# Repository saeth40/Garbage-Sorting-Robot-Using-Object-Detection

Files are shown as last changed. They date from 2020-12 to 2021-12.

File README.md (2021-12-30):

# Garbage-Sorting-Robot-Using-Object-Detection
2103499 Mechanical Engineering Project, Chulalongkorn University  2019-2020

***Advisor:*** Associate Professor Gridsada Phanomchoeng

***Objective:*** Improve the waste management in Thailand by creating a user-friendly robot that can automatically classify various types of garbage with high accuracy and work fast.

### A short demo VDO: [Click here](https://www.youtube.com/watch?v=DpFVvP5Zfqo).

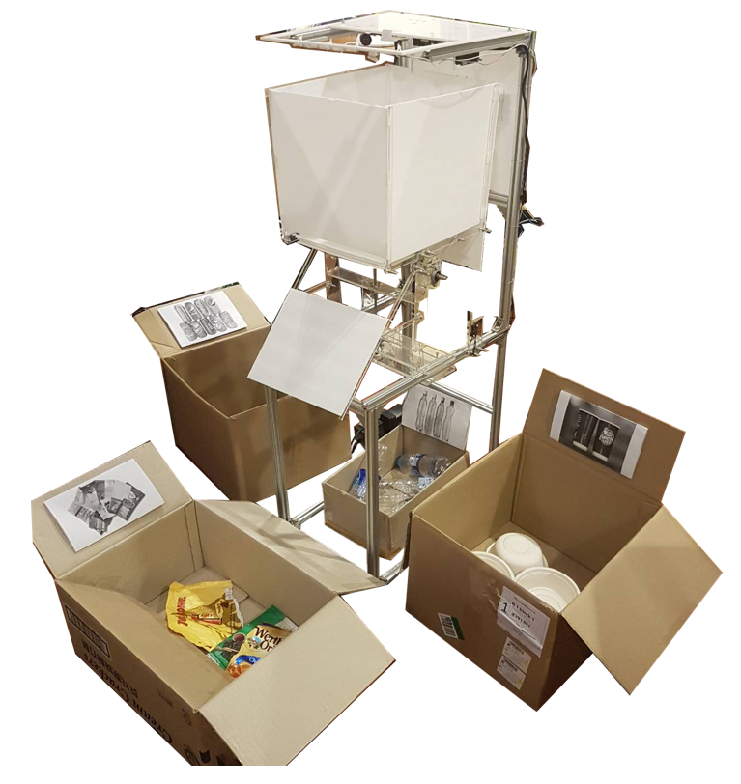
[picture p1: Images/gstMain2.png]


## Data collection
### 1. Types of garbage

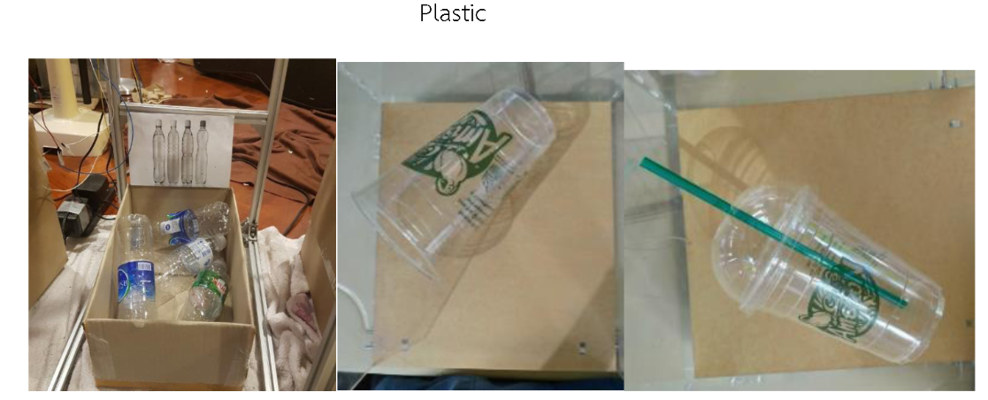
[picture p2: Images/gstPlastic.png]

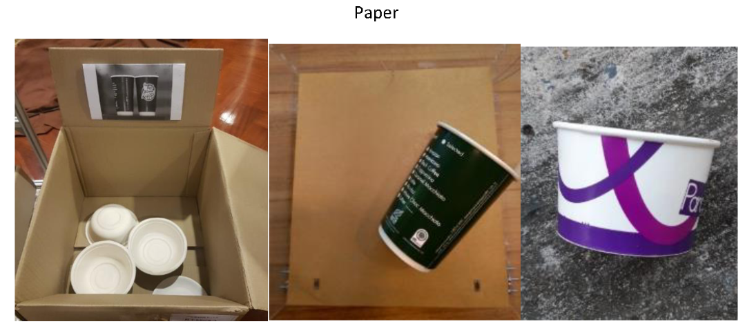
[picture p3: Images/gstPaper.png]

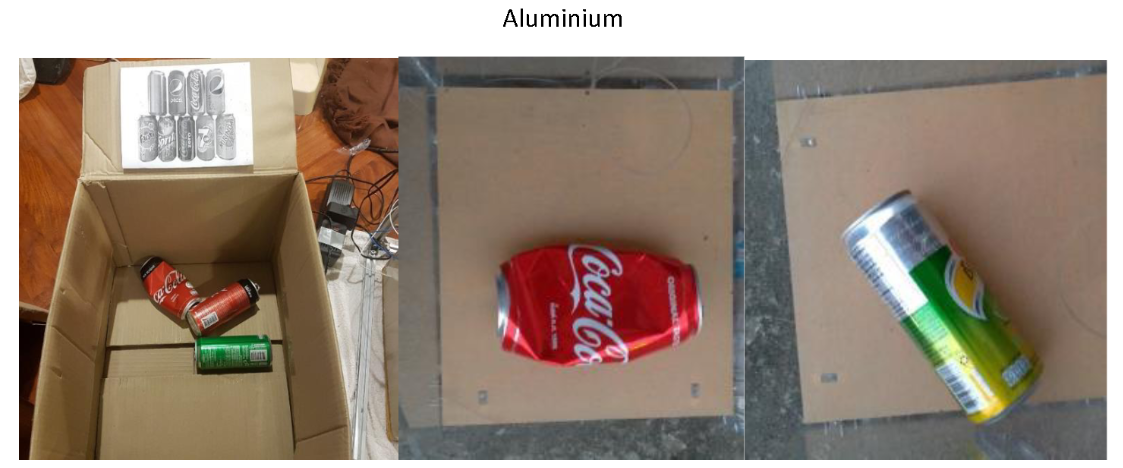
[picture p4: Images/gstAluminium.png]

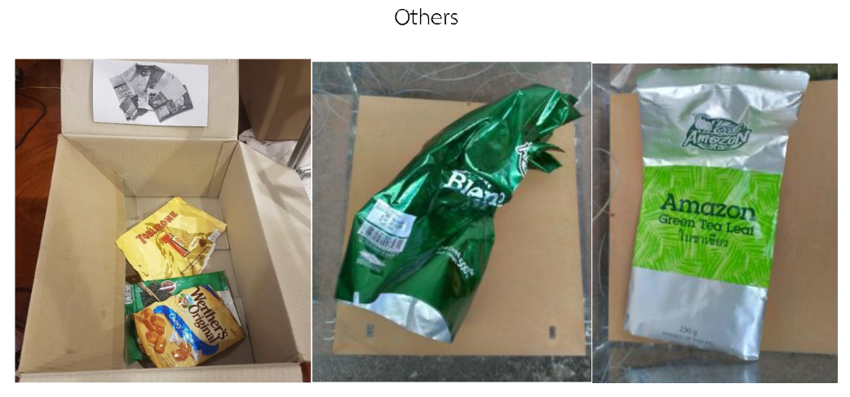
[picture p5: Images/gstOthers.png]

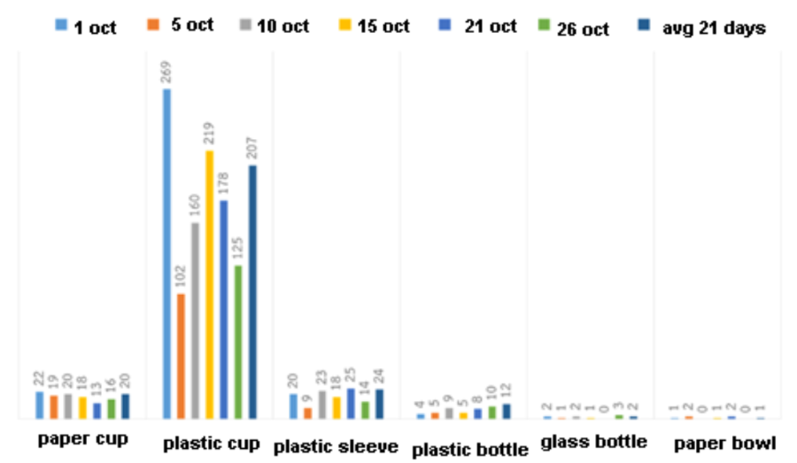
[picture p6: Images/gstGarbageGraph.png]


### 2. Users' preferences

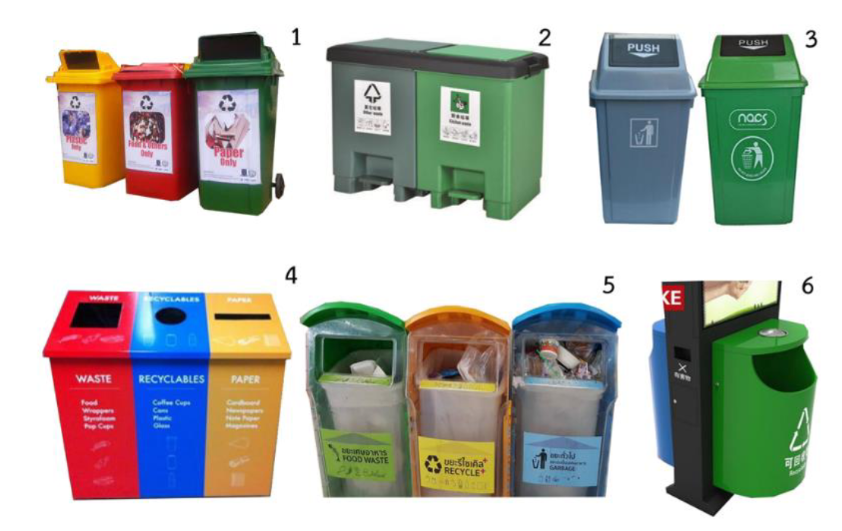
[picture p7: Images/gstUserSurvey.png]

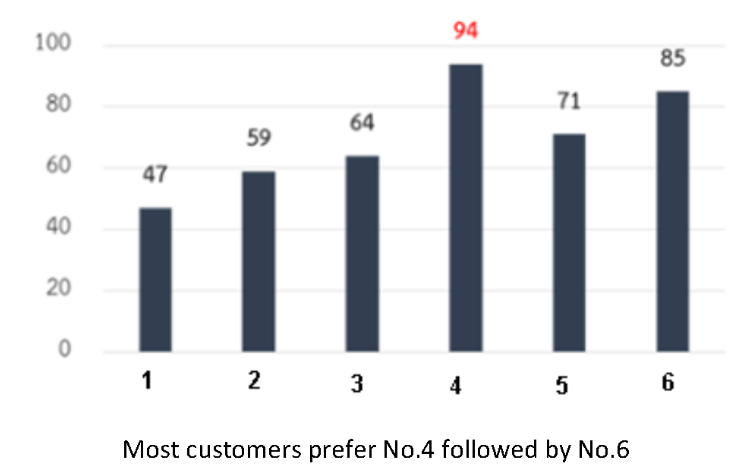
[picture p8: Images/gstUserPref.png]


### All details: [Data collection](https://github.com/saeth40/Garbage-Sorting-Robot-Using-Object-Detection/tree/main/Survey%20data)

## Design the robot

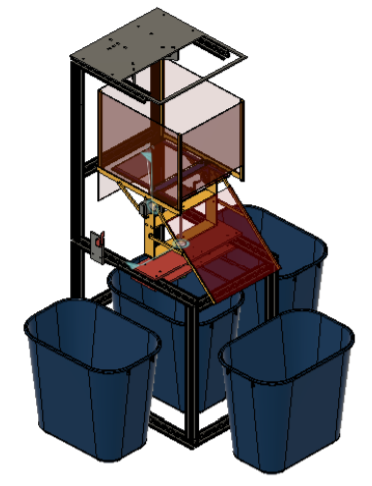
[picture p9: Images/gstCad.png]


### All details:
1. [related research papers](https://github.com/saeth40/Garbage-Sorting-Robot-Using-Object-Detection/tree/main/Related%20research%20papers)
2. [CAD design](https://github.com/saeth40/Garbage-Sorting-Robot-Using-Object-Detection/tree/main/CAD)
3. [List of equipment](https://github.com/saeth40/Garbage-Sorting-Robot-Using-Object-Detection/tree/main/Equipment)

## Programing and testing
### Training and testing object detection with Netpie IoT server to track system's behaviour

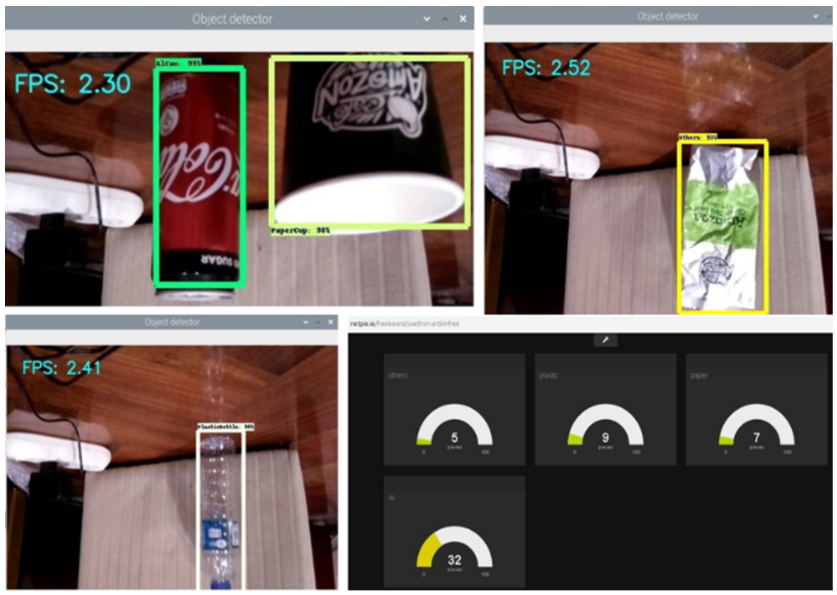
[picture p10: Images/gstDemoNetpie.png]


### Deploying model in the robot

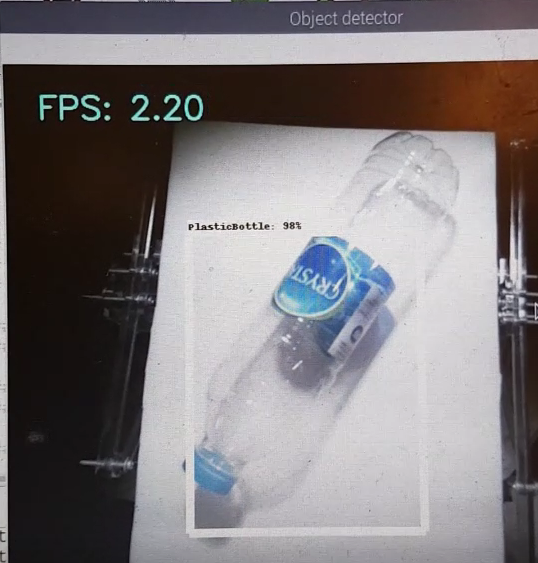
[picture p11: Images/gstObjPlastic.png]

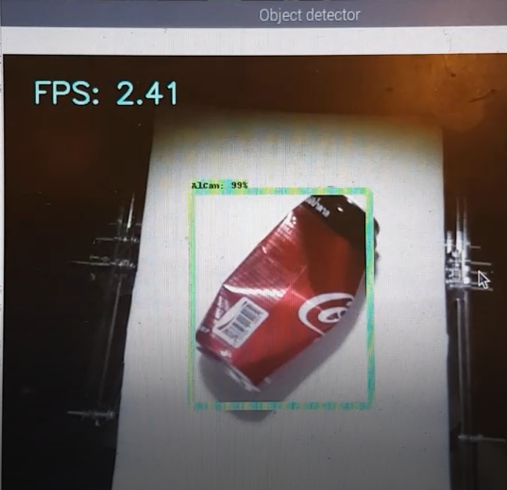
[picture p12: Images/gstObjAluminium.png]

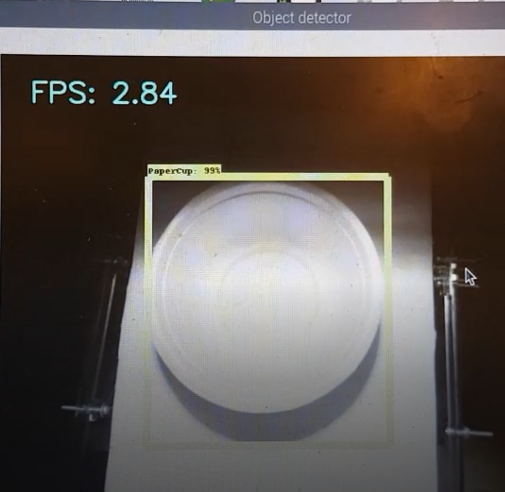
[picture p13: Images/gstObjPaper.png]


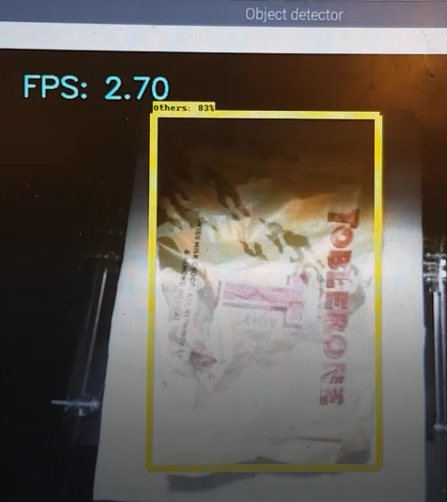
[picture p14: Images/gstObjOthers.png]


### All details
1. [Flowchart and wiring diagram](https://github.com/saeth40/Garbage-Sorting-Robot-Using-Object-Detection/tree/main/Flowchart%20and%20wiring%20diagram)
2. [C++ in Arduino to control sensors and actuators](https://github.com/saeth40/Garbage-Sorting-Robot-Using-Object-Detection/tree/main/C%20%2B%2B)
3. [Python to train and deploy object detection with IoT server](https://github.com/saeth40/Garbage-Sorting-Robot-Using-Object-Detection/tree/main/Python)
4. [Models used in this project](https://github.com/saeth40/Garbage-Sorting-Robot-Using-Object-Detection/tree/main/Python)
5. [Test results](https://github.com/saeth40/Garbage-Sorting-Robot-Using-Object-Detection/tree/main/Result)

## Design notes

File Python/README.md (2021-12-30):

# Object_detection_picamera

= sending the robot's data to NETPIE server + sending signals to Arduino

# objectDetecttionWithoutNETPIEwithOutGPIO

= not sending the robot's data to NETPIE server and not sending signals to Arduino

# objectDetecttionWithoutNETPIEwithGPIO

= sending the robot's data to NETPIE server but not sending signals to Arduino

# object_detection_tutorial

= tutorial in: https://github.com/saeth40/object_detection_demo

# Train_object_detection

= train the model used in this project

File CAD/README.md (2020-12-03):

You can open CAD files via Fusion360

The pdf file is the images of the CAD files and the real robot

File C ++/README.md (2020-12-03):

Open in Arduino IDE

You can download it from: https://www.arduino.cc/en/software 

This code is used in Arduino MEGA to communicate with Raspberry pi and control sensors and actuators

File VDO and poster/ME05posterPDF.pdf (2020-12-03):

# GARBAGE SORTER ROBOT FOR CAFÉ AMAZON

Saeth Wannasuphoprasit 5930504121 | Krittakorn Dilokpakin 5930009921 | Sittipat Kositpon 5930524721

### Associate Professor Gridsada Phanomchoeng, Ph.D. (Adviser) Department of Mechanical Engineering, Faculty of Engineering, Chulalongkorn University

The objective of this project is to design and build a trash separating robot with an image processing technique to identify types of trash. In this project, we mainly focus on the trash in café Amazon because of a huge amount and variety of trash along with an inappropriate waste management which leads to environmental degradation. Surveying types and quantity of trash in the actual location along with inspecting how people use bins, we can design the robot and identify types of trash to be separated by the robot. According to the pollution control department in Thailand, types of trash include compostable waste, recycle waste, non-degradable waste and dangerous waste.

## ABSTRACT

## Introduction

# HYULIC SYSTEM DESIGN

# RESULTS

Waste management is one of the biggest problems in the world. There are 14 million tons of trash per day in Thailand but approximately 70 percent of it are not managed and eliminated properly [1]. As a result, serious environment problems occur including air pollution from burnt trash, water pollution which are contaminated by trash, diseases spreading from dirty areas covered with trash and smelling problem. One of the most obvious causes of problems mentioned before is a mixture of all types of trash which leads to inefficient waste management. To solve this issue, waste separation from a trash separating robot improves waste management efficiency and reduces labors whose job is to separate trash. Moreover, useful waste such as recyclable trash can be utilized more for the green environment.

## Objective and scopes of the project

The main objectives of this project are as follows.
1. The robot can be installed in Amazon café.
2. The robot can separate recyclable trash including plastic bottles, aluminum cans, paper cups and other type of trash. The secondary objectives of this project are as follows.
1. The robot can identify food waste.
2. The robot can separate water and food from the packaging. The scopes of the project mainly focus on the trash from Amazon café because of a huge amount and variety of trash. Most importantly, the brand has many branches in Thailand so it is easy for us to get feedbacks from our users.

## Data collection

In order to design the robot, we need to know types and quantity of trash in Amazon café so we asked for those data (Fig. 1) from the Amazon café which is located near our faculty. After that, we collected some example of trash (Fig. 2). As a result, types of trash and the number of bins and robot’s specifications are identified.

Fig. 1 The amount of different types of waste in 21 days from the survey

## Design and Specification

Prototype 1 worked fine with it’s specifications with some cons as follows:
1. One trash per one cycle only 2. The tray could hit with the dome causing undesired motion
3. Untidy wiring 4. Hard to move the robot 5. The trash receiver opened and closed dangerously 6. Maximum time per cycle was 30 second and 7. Hard to upgrade in the future
Table 1 Efficiency of aluminum waste separation | Table 2 Efficiency of plastic waste separation

## Conclusion

Both prototype 1 and prototype 2 are acceptable in terms of the main objective of the project but Prototype 2 is better than the previous model in aspects mentioned in Results. However, both prototypes are not meet the requirements of the secondary objective. References

Fig. 2 Types of trash found in Amazon Café

## Results

### 2. Prototype 2

This prototype is the revised version of the previous one. The robot’s specifications are almost the same with the previous model with some additional features such as reduce operating time per 1 cycle, can increase number of bins in the future, reduce space required for installing the robot, save energy from unnecessary light required for the camera by using a relay, more precise positioning control and more user friendly. Operating cycle concepts remain the same (Fig. 5) but the robot’s mechanisms have been changed into a rotation of the tray instead of linear motion and limit switches for controlling the tray’s positions instead of using IR sensors. In addition, The main actuators are a DC motors for rotating the tray and a servo motor for adjusting the slope of the lifting plate. The positions of the bins are below the robot, in front of the robot, at the left side of the robot and at the right side of the robot as shown in Fig. 6.

## Design and Specification

### 1. Prototype 1

According to data collection, there were 4 bins which were categorized by types of trash (plastic, aluminum, paper and others). The robot’s specifications are automatic system, identifying trash using object detection [2], transferring trash into the right bin, system’s notifying, lighting, tracking system using Netpie, multiple trash prevention and easy to use. The main mechanisms were linear motion with a belt and lifting with a pulley driven by DC motors, IR sensors and an ultrasonic sensor to control the tray’s position and the slope of the lifting plate respectively and the servo motor for opening and closing a trash receiver as shown in Fig. 3. One cycle of operation include 1. Initial position ; The tray positioned at the dome and the lifting plate remained level to the ground. 2. Identifying trash. 3. driving the tray to the bin’s position and leaning the plate to dump the trash.
4. Returning to the initial position, the dome and tray design are displayed in Fig. 4.

Prototype 2 worked fine with it’s specifications with some improvement from the previous model as follows: 1. More accurate motion control 2. Smaller installing space 3. Faster operation (4.88 second per cycle in average) 5. More energy saving and 6. Can be upgraded in the future
The efficiency test in the prototype 2 was conducted to measure the accuracy of the separation system and the operating time per cycle. There were 4 sections which were divided into types of trash (aluminum, plastic, paper and others). Each section was divided into 3 thresholds which mean minimum percentages of the robot’s confidence to put the target trash into the right bin. The results are shown in table 1, 2, 3 and 4.

In terms of accuracy in 60%, 70% and 80% threshold, aluminum had the accuracy of 8/10 6/10 and 10/10 respectively, plastic had the accuracy of 10/10, 9/10 and 7/10 respectively, paper had the accuracy of 10/10 in all thresholds and others had the accuracy of 6/10 3/10 and 5/10 respectively. It can be concluded from the results that the average operating time per cycle of the entire system was 4.88 second. The average operating time per cycle of aluminum, plastic, paper and others were 5, 4.85, 6.08 and 3.57 second respectively. In terms of threshold, 80% was suitable for aluminum as the other two had some errors identifying the object, 60% to 70% was suitable for plastic as the confidence rate sometimes didn’t reach 80%. All thresholds were suitable for paper as there were no sign of errors and less than 60% was suitable for others as there were sign of errors in every thresholds.

1. “ปัญหาสิ่งแวดล้อมจากขยะมูลฝอย” กรมควบคุมมลพิษ. Accessed October 31, 2019. http://www.pcd.go.th/info_serv/waste_rubbish.htm
2. “Object detection”. Accessed April 11, 2020. https://en.wikipedia.org/wiki/Object_detection
Fig. 3 The mechanism of the prototype 1 robot | Fig. 4 Design of tray and dome of prototype 1 in Fusion360
Fig. 5 Schematic of the program | Fig. 6 The actual operation of the robot
Table 3 Efficiency of paper waste separation | Table 4 Efficiency of other waste separation

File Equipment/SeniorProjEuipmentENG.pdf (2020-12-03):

### 1. Nucleo-F411RE [10]

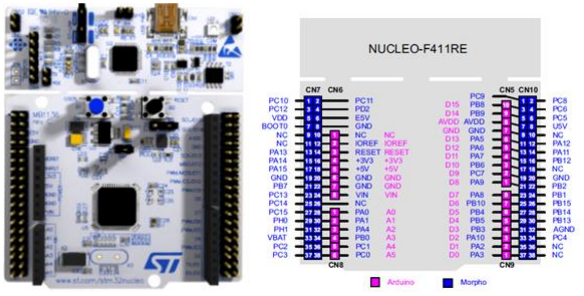
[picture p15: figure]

Specifications
1. Board connectors: External SMPS experimentation dedicated connector
2. Micro-AB or Mini-AB USB connector for the ST-LINK
3. MIPI® debug connector
4. System requirements: Windows® OS (7, 8 and 10), Linux® 64-bit, or macOS®
5. Price: 650 ฿

### 2. Raspberry Pi 4 Model B [11]

Specifications

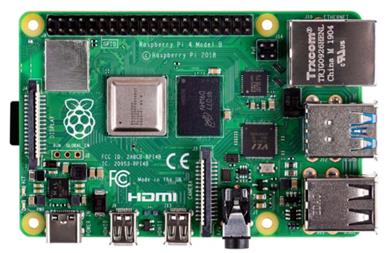
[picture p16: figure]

1. Processor: Broadcom BCM2711, quad-core Cortex-A72 (ARM v8) 64-bit SoC @ 1.5GHz
2. Connectivity:
1. 2.4 GHz and 5.0 GHz IEEE 802.11b/g/n/ac wireless
2. LAN
3. Bluetooth 5.0, BLE
4. Gigabit Ethernet
5. 2 × USB 3.0 ports, 2 × USB 2.0 ports.
3. Video & sound:
1. 2 × micro HDMI ports (up to 4Kp60 supported)
2. 2-lane MIPI DSI display port
3. 2-lane MIPI CSI camera port
4. 4-pole stereo audio and composite video port
4. Multimedia:
1. H.265 (4Kp60 decode);
2. H.264 (1080p60 decode, 1080p30 encode);
3. OpenGL ES, 3.0 graphics
5. SD card support: Micro SD card slot for loading operating system and data storage

6. Input power:
1. 5V DC via USB-C connector (minimum 3A)
2. 5V DC via GPIO header (minimum 3A)
3. Power over Ethernet (PoE)–enabled (requires separate PoE HAT)
7. Environment: Operating temperature 0–50ºC
8. Price: 2,595 ฿

### 3. Raspberry Pi Camera Module v1 [12]

Specifications
1. Sensor: Sony IMX219
2. Resolution: 8 Megapixels (3280 × 2464 pixels)
3. Video modes: 1080p30, 720p60 and 640 × 480p60/90
4. Focal length: 3.04 mm
5. Horizontal field of view: 62.2 degrees
6. Vertical field of view: 48.8 degrees
7. Focal ratio (F-Stop): 2.0
8. Weight: 3 g
9. Price: 989 ฿

### 4. SG90 Micro Servo [13]

Specifications

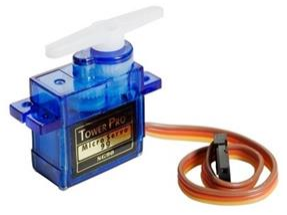
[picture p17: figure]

1. Operating Voltage: 5V
2. Torque: 2.5kg/cm
3. Operating speed is 0.1s/60°
4. Rotation: 0°-180°
5. Weight of motor: 9 g
6. Price: 90 ฿

### 5. DC Gear Box Motor 12V [14]

Specifications

1. Motor Diameter: 37 mm
2. Motor Shaft: 6mm
3. Torque: 3.95-13.5 kg cm
4. Price: 380 ฿

### 6. Infrared Sensor Switch (E18-D80NK-N) [15]

Specifications
1. Range: 6-80 cm
2. Operating Voltage: 5V
3. Price: 144 ฿

### 7. Ultrasonic sensors (HY-SRF05) [16]

Specifications

1. Operating Voltage: 5V
2. Sensor Angle: 15 Degree
3. Detection distance: 2-450 cm
4. Precision: 2 mm
5. Price: 70 ฿

### 8. Limit Switch (V-153-1C25) [17]

Specifications
1. 0.3A at 250VDC
2. Maximum Operating Force: 1.96 N
3. Price: 15 ฿

### 9 L298N Dual H-Bridge Motor Driver [18]

Specifications

1. Input Voltage: 3.2 – 40 VDC
2. Power Supply: 5 - 35 VDC
3. Peak current: 2 A
4. Operating current range: 0 – 36 mA
5. Control signal input voltage range:
1. Low: -0.3V ≤ Vin ≤ 1.5V
2. High: 2.3V ≤ Vin ≤ Vss.
6. Storage temperature: -25 oC ~ +130 oC
7. Price: 130 ฿

10. 5V Fan [19]

Specifications

1. Dimensions: 60x60x10mm
2. Rated Voltage: 5V
3. Rated Current: 0.25A
4. Speed: 2900RPM
5. Weight: 35g
6. Price: 120 ฿
11. 5mm LED [20]

### 12. LED Flexible Strip 5630 Series [21]

Specifications

1. Power Rating 75 W / 5 m
2. Light Angle: 120 Degree
3. Brightness: 55-62 lm
13. 0.25W 5% Carbon Filmed Resistor [22]

### 14. Belt set [23]

### 15. Shaft 8mm 50cm [24]

Specifications
1. diameter 8mm
2. stainless steel
3. length: 50cm
4. price 120 THB

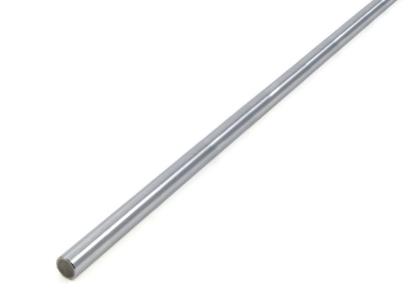
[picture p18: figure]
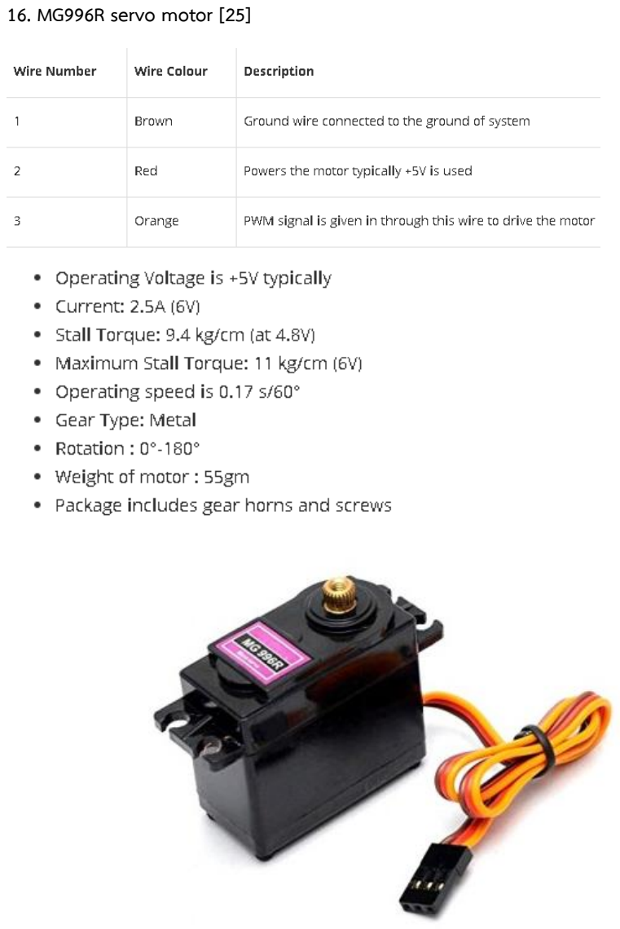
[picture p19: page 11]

### 16. MG996R servo motor [25]

### 17. Bearing 8mm [26]

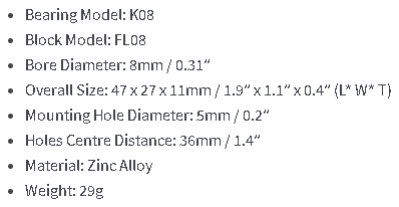
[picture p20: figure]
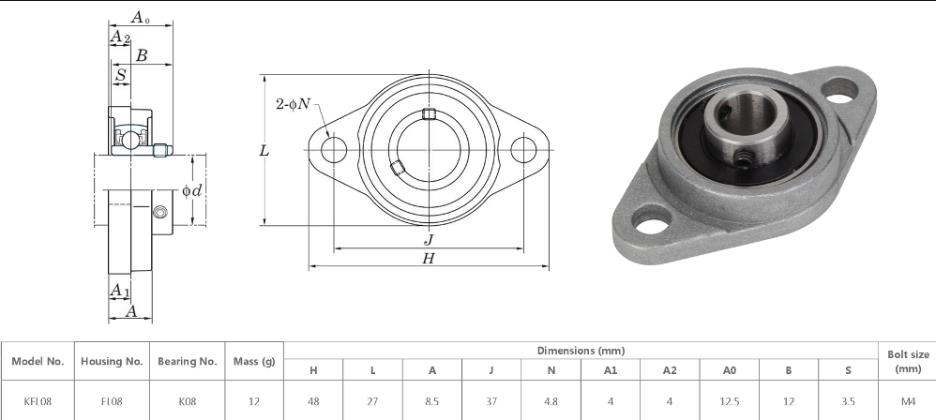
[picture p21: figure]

### 18. Thrust Ball Bearing 8mm [27]

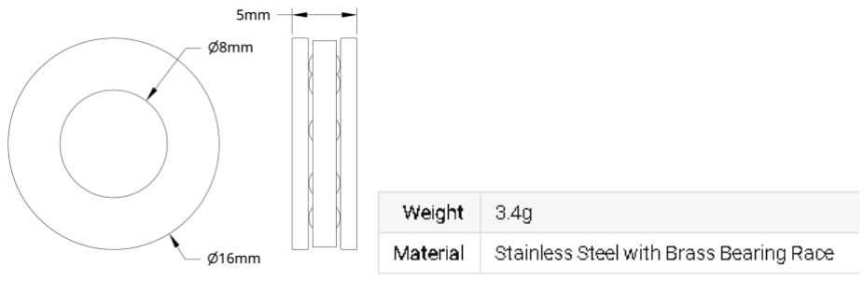
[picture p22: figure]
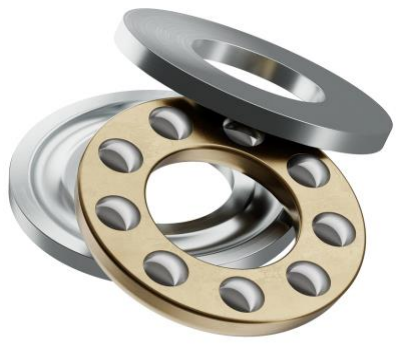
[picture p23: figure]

19. 8mm Lock Collar [28]

### 20. Single channel 5v relay [29]

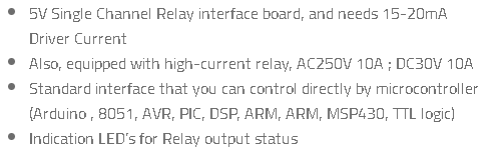
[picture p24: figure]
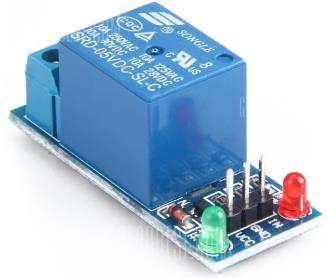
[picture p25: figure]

21. 5v ac to dc adaptor [30]

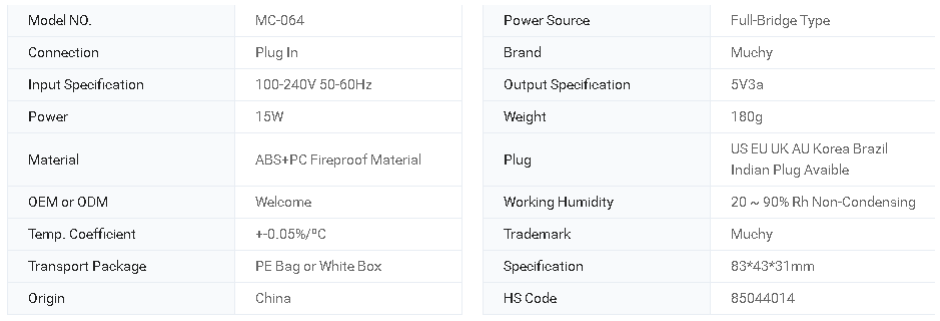
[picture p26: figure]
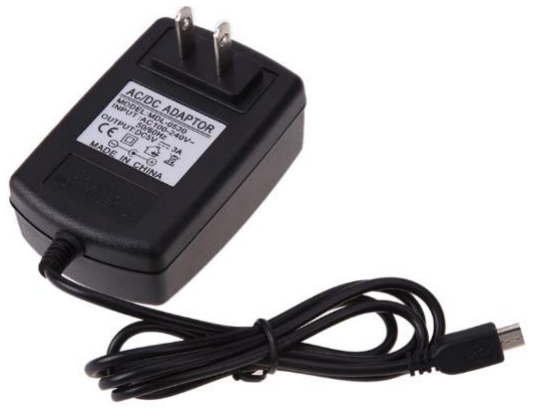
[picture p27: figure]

22. 12v ac to dc adaptor [31]

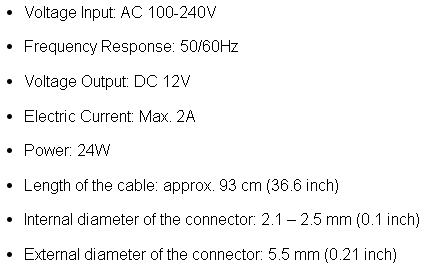
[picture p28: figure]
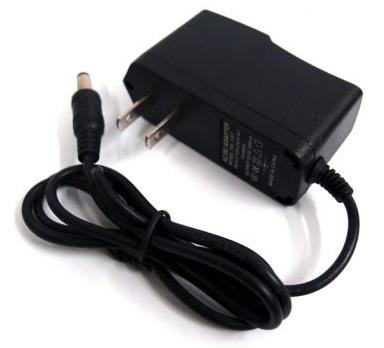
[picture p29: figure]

### 23. Coupling 6mm to 8mm [32]

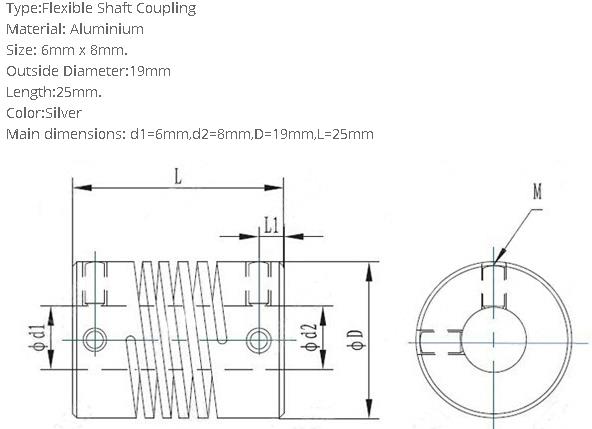
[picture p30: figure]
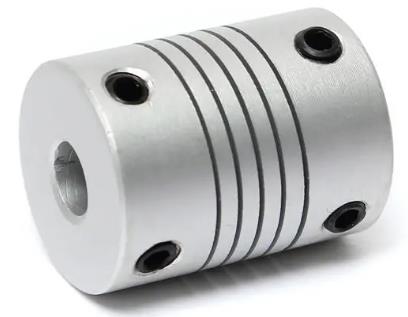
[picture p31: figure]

### 24. Flange 8mm [33]

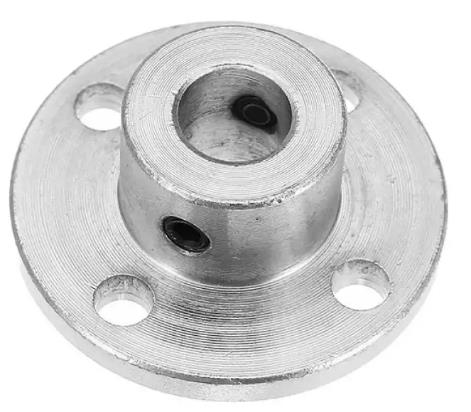
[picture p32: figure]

25. 20x20 Aluminum profile [34]

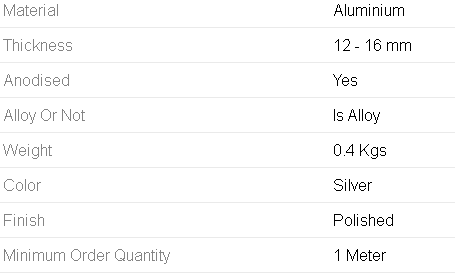
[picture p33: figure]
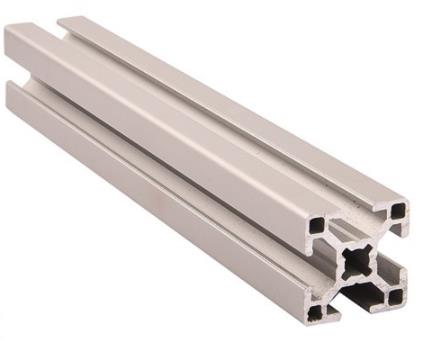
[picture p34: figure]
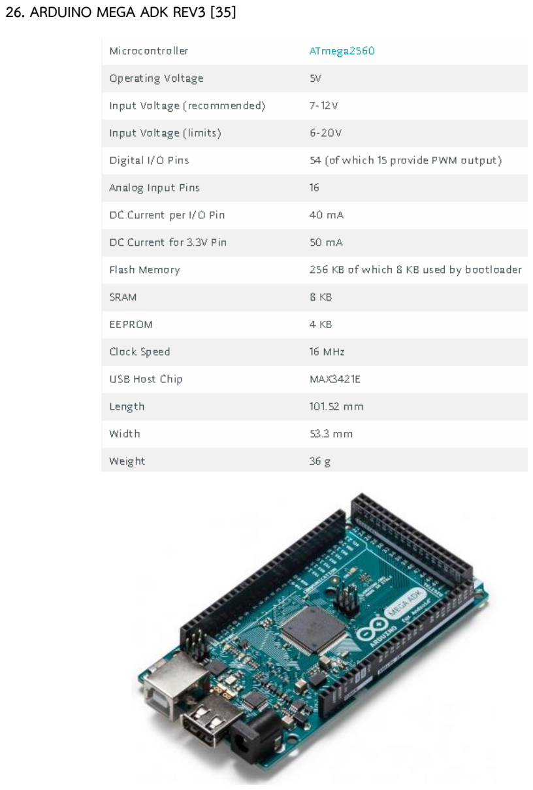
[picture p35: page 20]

### 26. ARDUINO MEGA ADK REV3 [35]

### 26. Others

Acrylic 5mm, 8mm

Wood

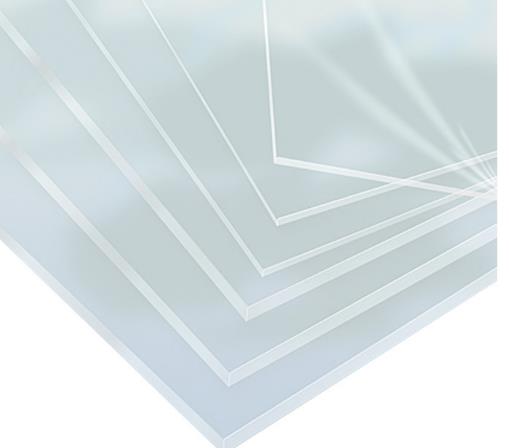
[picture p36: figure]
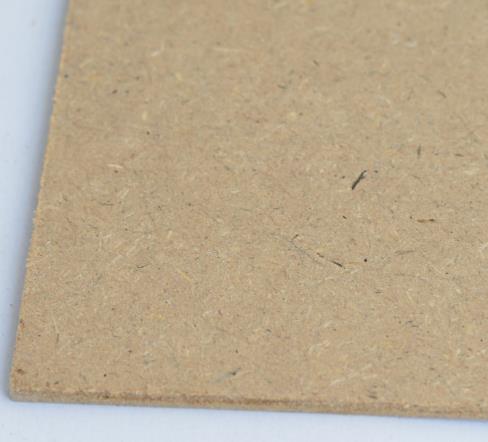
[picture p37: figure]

Future board 2mm

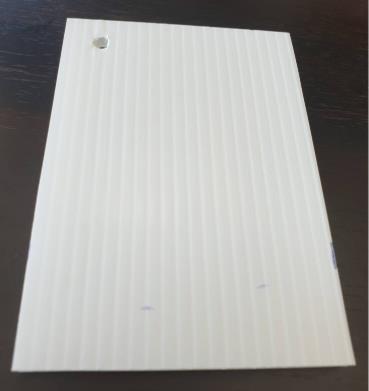
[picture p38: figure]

### References

10. “NUCLEO-F411RE.” STMicroelectronics. Accessed December 4, 2019. https://www.st.com/en/evaluation-tools/nucleo-f411re.html.
11. “Buy a Raspberry Pi 4 Model B – Raspberry Pi.” Buy a Raspberry Pi 4 Model B – Raspberry Pi. Accessed December 4, 2019. https://www.raspberrypi.org/products/raspberrypi-4-model-b/.
12. “Camera Module.” Camera Module - Raspberry Pi Documentation. Accessed December 4, 2019. https://www.raspberrypi.org/documentation/hardware/camera/.
13. “Servo Motor SG-90 Basics, Pinout, Wire Description, Datasheet.” Basics, Pinout, Wire Description, Datasheet. Accessed December 4, 2019. https://components101.com/servomotor-basics-pinout-datasheet.
14. “1x มอเตอร์เกียร์ดีซี 12V 10 Rpm ขนาด 37 มม. แกน 6 มม. Zhengke.” micontechlab. Accessed December 4, 2019. http://www.micontechlab.com/product/1271/1x-มอเตอร์เกียร์ดี ซี-12v-10-rpm-ขนาด-37-มม-แกน-6-มม-zhengke.
15. ‘IR sensor’. Accessed December 4, 2019. http://www.ett.co.th/productSensor/E18-D80NK/E18-D80NK.html.
16. Dejan, Dejan Nedelkovski, Dejan Nedelkovski, Dejan Nedelkovski, Siddharth, Dejan Nedelkovski February, Dejan Nedelkovski, et al. “Ultrasonic Sensor HC-SR04 and Arduino Tutorial.” HowToMechatronics, August 4, 2018. https://howtomechatronics.com/tutorials/arduino/ultrasonic-sensor-hc-sr04/.
17. GOH, Tomi. “Arduino Uno Limit Switch Interfacing and Programming.” Electronic Clinic, October 26, 2019. https://www.electroniclinic.com/arduino-uno-limit-switch-tutorial/.
18. Darko, Luis, Janos Szeman, Andras Tantos, Alex, Andras Tantos, Andras Tantos, et al. Modular Circuits. Accessed December 4, 2019. https://www.modularcircuits.com/blog/articles/h-bridge-secrets/h-bridges-the-basics/.

19. “5 Volt Fans: Get the Right 5 Volt Cooling Fan at Coolerguys %Removeshopname%.” Coolerguys. Accessed December 4, 2019. https://www.coolerguys.com/collections/dc-5-volt-fans.
20. “Make a Simple LED Circuit.” Arduino Project Hub. Accessed December 4, 2019. https://create.arduino.cc/projecthub/rowan07/make-a-simple-led-circuit-ce8308.
21. “LemonBest - (Cool) 5630 5M White 300 SMD 12V LED Flexible Strip Light Waterproof.” English. Accessed December 4, 2019. https://www.lemonbest.com/lemonbest-cool-5630-5m-white-300-smd-12v-led-flexible-strip-light-waterproof.
22. “Electronics & Robotics Parts Online Store.” Udvabony.com, September 27, 2019. https://udvabony.com/.
23. “Replace a Timing Belt - Replacement Avoids Costly Repairs.” Meineke, October 22, 2019. https://www.meineke.com/blog/replace-timing-belt/.
24. “8mm - Hard Chrome Plated Steel Shaft - 1025.” 8mm - 50cm Hard Chrome Plated
Stainless Steel Shaft - 1025 | RED CNC: Build Smart Machines. Accessed April 10, 2020.
https://www.redcnc.com/p-hard-chrome-plated-steel-shaft-15.
25. “MG996R Servo Motor Datasheet, Wiring Diagram & Features.” Datasheet, Wiring Diagram & Features. Accessed April 10, 2020. https://components101.com/motors/mg996r-servomotor-datasheet.
26. “KFL08 Pillow Block Flange Bearing.” Maker Store USA. Accessed April 10, 2020. http://makerstore.cc/product/kfl08-pillow-block-flange-bearing/.
27. “1613 Series Thrust Ball Bearing (8mm ID x 16mm OD, 5mm Thickness).” goBILDA. Accessed April 10, 2020. https://www.gobilda.com/1613-series-thrust-ball-bearing-8mm-id-x-16mm-od-5mm-thickness/.

28. “8mm Lock Collar T8 Lead Screw Lock Ring Lock Block For 3D Printer 3D Printer & Supplies from Electronics on Banggood.com.” www.banggood.com. Accessed April 10, 2020. https://www.banggood.com/8mm-Lock-Collar-T8-Lead-Screw-Lock-Ring-Lock-Block-For-3D-Printer-p-1245112.html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.
29. “Single Channel 5V Relay.” TD Egypt. Accessed April 10, 2020. https://www.tdegypt.com/product/single-channel-5v-relay/.
30. “5V 3A DC Adapter with UL ROHS CB SAA Certificate.” Made. Accessed April 10, 2020. https://maichi.en.made-in-china.com/product/KCIElONGSDVd/China-5V-3A-DC-Adapter-With-UL-ROHS-CB-SAA-Certificate.html.
31. “12V Power Adapter: Makerlab Electronics.” Makerlab Electronics - Bits and pieces of Hardware and Electronic Stuffs! Accessed April 10, 2020. https://www.makerlabelectronics.com/product/12v-2a-power-adapter/.
32. “6mm x 8mm Aluminum Flexible Shaft Coupling OD19mm x L25mm, Industrial & Scientific.” www.banggood.com. Accessed April 10, 2020. https://www.banggood.com/6mmx-8mm-Aluminum-Flexible-Shaft-Coupling-OD19mm-x-L25mm-CNC-Stepper-Motor-Coupler-Connector-p-994358.html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.
33. “8mm Flange Coupling Motor For CNC.” Electronics.Com.BD. Accessed April 10, 2020. https://www.electronics.com.bd/8mm-Flange-Coupling-Motor-For-CNC.
34. “20x20 Aluminium Profile.” indiamart.com. Accessed April 10, 2020. https://www.indiamart.com/proddetail/20x20-aluminium-profile-16628862262.html.
35. ‘Arduino Mega ADK Rev3’. Accessed April 10, 2020. https://store.arduino.cc/usa/arduinomega-adk-rev3.

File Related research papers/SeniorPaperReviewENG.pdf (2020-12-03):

### List of related research papers

1. Developing an Intelligent Waste Sorting System with Robotic Arm: A Step towards Green Environment [1]
2. Artificial Intelligence in Automated Sorting in Trash Recycling [2]
3. Development of Automatic Smart Waste Sorter Machine [3]
4. Waste Segregation Using Machine Learning (journal) [4]
5. Classification of Recyclables from E-Waste Stream Using Thermal Imaging-Based Technique [5]
6. Smart Bin Implementation for Smart City [6]
7. The Design and Implementation of Smart Trash Bin [7]
8. Intelligent Waste Separator [8]
9. Smart Bin: Internet-of-Things Garbage Monitoring System [9]

Paper | Name | Principle | Pros | Cons
1 | Developing an Intelligent Waste Sorting System with Robotic Arm | Use a robot’s arm to pick trash into a belt and use - voltage sensor to detect food - IR sensor to find trash - inductive sensor to detect metal | 1.cheap 2.Automatic arm 3.mobile app | 1.1 trash per operation 2.inaccurate sensors
2 | Artificial Intelligence in Automated Sorting in Trash Recycling | Test many Machine learning algorithms to find the best one with the highest accuracy | 1.CNN is the most accurate one | 1.time consuming 2.inaccurate with glass
3 | Development of Automatic Smart Waste Sorter Machine | - IR sensors for detection trash - metal sensor - glass sensor - laser and LDR for separating paper and transparent plastic | 1.cheap 2.automatic system | 1.slow 2.unable to classify organic waste
4 | WasteSegregati on Using Machine Learning (journal) | Use raspberry pi and pi cam for object detection, then use a robot’s arm to transfer compossible and incompossible trash into 2 bins | 1.automatic 2.no sensors 3.upgradable | 1.limited types of trash (2) 2.awful delay
5 | Classificationof Recyclables from E-Waste Stream Using Thermal Imaging-Based Technique | Use thermal imaging technique and SVM to classify recycle trash from electronics waste by inspecting radiation when received head from hot chamber | 1.no external disturbance 2. work well with bad condition i.e. lot of dust | 1.need light power 2. work only in the specific areas 3.temp control in hot chamber
Paper | Name | Principle | Pros | Cons
6 | SmartBin Implementatio n for Smart City | use level sensor to measure trash level in bins and GSM, IOT to send SMS, GPS of full bins to trash keepers | 1.simple 2. real time | 1.can’t separate trash
7 | The Design and Implementatio n of Smart Trash Bin | Use Ultrasonic sensors to detect trash level in bins and send SMS to report trash keepers. | 1.cheap 2.solar cell | 1.can’t separate trash

8 | IntelligentWast e Separator | Transfer images into grey scale images and use servo motors to deliver trash into bins | 1.high accuracy 2.simple | 1.1 trash per operation 2.can’t work with irregular trash
9 | SmartBin: Internet-of-Things Garbage Monitoring System | Use Ultrasonic sensors to measure trash level in bins and use Thinspeak to send data via IOT | 1.real time 2.IOT | 1.can’t separate trash

### References

1. ‘Developing an Intelligent Waste Sorting System with Robotic Arm: A Step towards Green Environment’, Accessed December 4,
2019.https://www.researchgate.net/publication/331110386_Developing_an_Intelligent_Waste_Sorting_System_with_Robotic_Arm_A_Step_towards_Green_Environment
2. ‘Artificial Intelligence in Automated Sorting in Trash Recycling’, Accessed December 4, 2019.https://www.researchgate.net/publication/330350735_Artificial_Intelligence_in_Automated_Sorting_in_Trash_Re cycling
3. ‘Development of Automatic Smart Waste Sorter Machine’, Accessed December 5, 2019.https://www.researchgate.net/publication/271964625_Development_of_Automatic_Smart_Waste_Sorter_Machi ne
4. ‘Waste Segregation Using Machine Learning’, Accessed December 5, 2019.https://www.ijraset.com/fileserve.php?FID=14058
5. ‘Classification of Recyclables from E-Waste Stream Using Thermal Imaging-Based Technique’, Accessed December 6, 2019. https://www.researchgate.net/publication/330512713_Classification_of_Recyclables_from_E-Waste_Stream_Using_Thermal_Imaging-Based_Technique
6. ‘Smart Bin Implementation for Smart City’, Accessed December 7, 2019. https://ijarcce.com/upload/2017/april-17/IJARCCE%20143.pdf

7.’ The Design and Implementation of Smart Trash Bin’, Accessed December 7, 2019.https://www.researchgate.net/publication/319381573_The_Design_and_Implementation_of_Smart_Trash_Bin

8. ‘Intelligent Waste Separator’, Accessed December 7, 2019.https://www.researchgate.net/publication/285611174_Intelligent_Waste_Separator
9. ‘Smart Bin: Internet-of-Things Garbage Monitoring System’. Accessed December 8, 2019. https://www.researchgate.net/publication/321725917_Smart_Bin_Internet-of-Things_Garbage_Monitoring_System

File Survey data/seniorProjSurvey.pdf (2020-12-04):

## Data collection

### 1. Garbage


6 types of purchased packages for 21 days in Amazon café

We can see that customers prefer buying plastic cups in the café

Real images of all garbage in the café which were categorized into plastic, aluminium, paper and other

## Images in a testing (the first left) and training process

## Plastic


Paper

Aluminium

## Others


### 2. Users’ preferences

First, we surveyed customers to find the best design from 6 candidates

Most customers prefer No.4 followed by No.6


No.4 design

Then we asked them to answer this Thai survey

Results from the Thai survey:

most customers don’t want their hand to be dirty when they drop trash into bins

sometime bins are full of trash and they are unable to put another one in it

most of them want to separate trash for environmental reasons

Another thing we wanted to know is about mechanism. So , we asked them to choose 4 types of mechanism:

1. open bins with their hand and drop trash into it (use their hands)
2. press a button next to a bin to open the bin (buttons)
3. drop trash directly into bins (simple drop)
4. scan trash first outside bins and then drop it into the appropriate bin (scan first)


Most customers prefer simple usage (just drop trash into bins) followed by using buttons

### 3. Summary:

Plastic is the most common type of recycle trash

We chose to classify 4 types of trash (plastic, paper, aluminium and others)

Most users prefer bins that are simple to use (without using their hands to open it and let their hands dirty)


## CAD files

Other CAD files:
CAD/design2ver4 v30 (1).f3z

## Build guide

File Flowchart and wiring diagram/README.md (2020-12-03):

The pdf file shows flow chart, wiring diagram and Raspberry pi 4 GPIO

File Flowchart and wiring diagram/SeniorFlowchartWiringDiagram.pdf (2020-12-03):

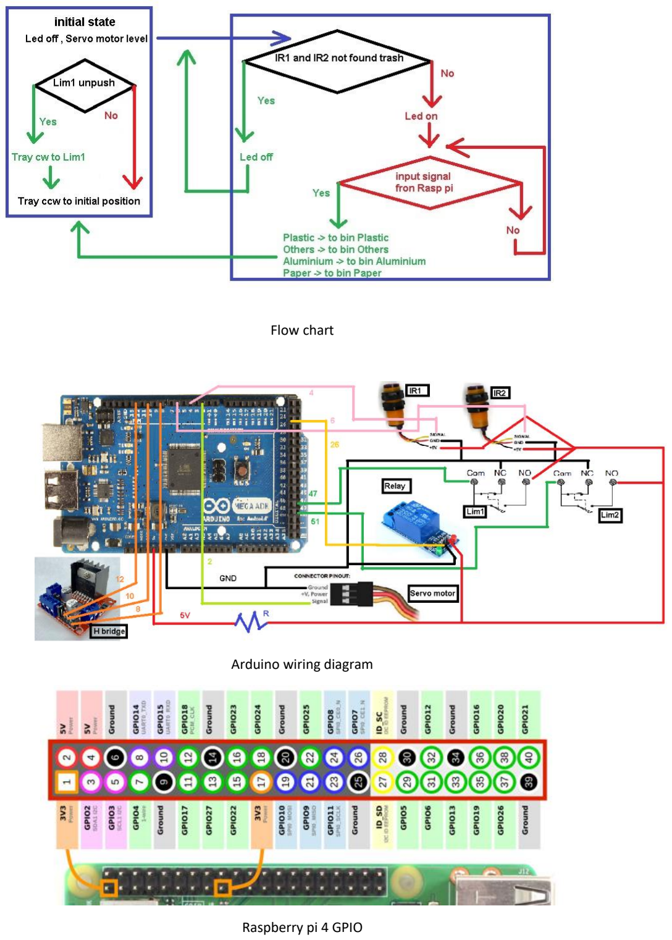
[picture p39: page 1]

Flow chart

Arduino wiring diagram

Raspberry pi 4 GPIO

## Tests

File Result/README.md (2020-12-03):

The pdf file explains all test methods and results

The exel file is raw data

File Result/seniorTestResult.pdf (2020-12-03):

### Test result

We tested 4 types of trash (aluminium, plastic, paper and others) with 3 different threshold (60%, 70% and 80%) and captured operation time. Percentage of threshold means the minimum percentage of the model’s confidence in order to classify the desired type of trash. i.e. the model with the 65% of confidence in ‘paper’ will be able to classify paper with the 60% of threshold but unable to perform this task at 70% and 80% threshold.

### 1. Aluminium

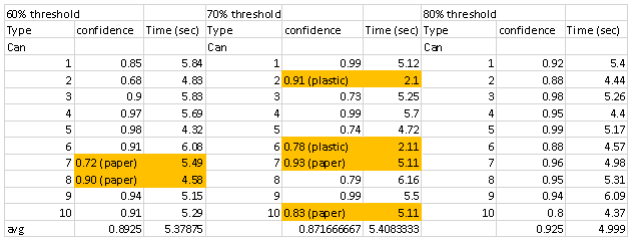
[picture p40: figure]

Result: performed good in 80% threshold with some minor error in the other threshold. The average time was about 5 second per operation. The overall accuracy was 80%.

### 2. Plastic

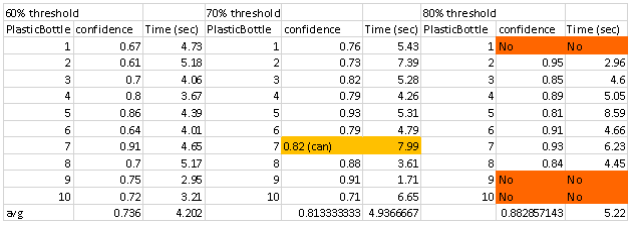
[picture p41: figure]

Result: performed good only in 60% threshold. There were some error in 70% threshold and some missing detection in the last threshold. The overall accuracy was 86.67% and the overall operation time per cycle was 5.22 second.

### 3. Paper

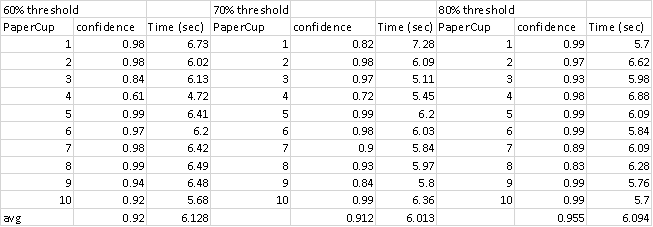
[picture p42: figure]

Result: no error at all (100% accuracy) and the average time per operation was 6.09 second.

### 4. Others

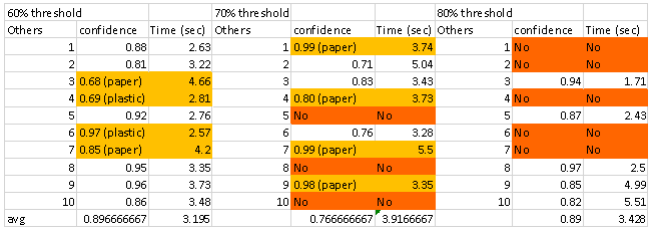
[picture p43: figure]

Result: there were many errors in every threshold. Missing detection occurred in 70% and 80% threshold. The average accuracy was 46.67% and the average time per operation was 3.43 second

Overall, aluminium performed good at more than 80% threshold where as plastic performed better at lower threshold (lower than 70%). Paper performed good in all situation where as Others could be better when performed in low threshold (lower than 60% threshold). The overall accuracy of the model was 89% accuracy with the average time per operation in 5 second.

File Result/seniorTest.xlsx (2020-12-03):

60% threshold |  |  | 70% threshold |  |  | 80% threshold
Type | confidence | Time (sec) | Type | confidence | Time (sec) | Type | confidence | Time (sec)
Can |  |  | Can |  |  | Can
1 | 0.85 | 5.84 | 1 | 0.99 | 5.12 | 1 | 0.92 | 5.4
2 | 0.68 | 4.83 | 2 | 0.91 (plastic) | 2.1 | 2 | 0.88 | 4.44
3 | 0.9 | 5.83 | 3 | 0.73 | 5.25 | 3 | 0.98 | 5.26
4 | 0.97 | 5.69 | 4 | 0.99 | 5.7 | 4 | 0.95 | 4.4
5 | 0.98 | 4.32 | 5 | 0.74 | 4.72 | 5 | 0.99 | 5.17
6 | 0.91 | 6.08 | 6 | 0.78 (plastic) | 2.11 | 6 | 0.88 | 4.57
7 | 0.72 (paper) | 5.49 | 7 | 0.93 (paper) | 5.11 | 7 | 0.96 | 4.98
8 | 0.90 (paper) | 4.58 | 8 | 0.79 | 6.16 | 8 | 0.95 | 5.31
9 | 0.94 | 5.15 | 9 | 0.99 | 5.5 | 9 | 0.94 | 6.09
10 | 0.91 | 5.29 | 10 | 0.83 (paper) | 5.11 | 10 | 0.8 | 4.37 | time avg
avg | 0.8925 | 5.37875 |  | 0.8716666667 | 5.408333333 |  | 0.925 | 4.999 | 4.999
60% threshold |  |  | 70% threshold |  |  | 80% threshold
PlasticBottle | confidence | Time (sec) | PlasticBottle | confidence | Time (sec) | PlasticBottle | confidence | Time (sec)
1 | 0.67 | 4.73 | 1 | 0.76 | 5.43 | 1 | No | No
2 | 0.61 | 5.18 | 2 | 0.73 | 7.39 | 2 | 0.95 | 2.96
3 | 0.7 | 4.06 | 3 | 0.82 | 5.28 | 3 | 0.85 | 4.6
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

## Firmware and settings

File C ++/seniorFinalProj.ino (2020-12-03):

//Servo setup
//remote destop:run, mstsc, ip 
//user: pi, pass : service
//rasp gpio : 12(al),26(others),15(paper),7(plastic)
#include <Servo.h>
Servo myservo;
// defines pins numbers, pwm: 2-13
const int LedPlas = 31; //d1, 7 to 31
const int LedAl = 35; //d2, 12 to 35
const int LedPaper = 39; //d3, 15 to 39
const int LedOthers = 43; //d4, 26 to 43
const int  servo = 2; //d5
const int Lim1 = 47; //d6, cw
const int Lim2 = 51; //d7, ccw
const int Ir1 = 4; //d8
const int Ir2 = 6; //d9
const int Hb1 = 8; //d10
const int Hb2 = 10; //d11
const int HbPwm = 12;//pwm1 
const int Relay = 26; //d12
//for while true loop
int assume=0;
int assume2=0;
int tohome = 1200;
void setup() {
  // put your setup code here, to run once:
  pinMode(LedPlas, INPUT);
  pinMode(LedAl, INPUT);
  pinMode(LedPaper, INPUT);
  pinMode(LedOthers, INPUT);
  myservo.attach(servo);
  pinMode(Lim1, INPUT);
  pinMode(Lim2, INPUT);
  pinMode(Ir1, INPUT);
  pinMode(Ir2, INPUT);
  pinMode(Hb1, OUTPUT);
  pinMode(Hb2, OUTPUT);
  pinMode(HbPwm, OUTPUT);
  pinMode(Relay, OUTPUT);

}

void loop() {
  //set initial position
  digitalWrite(Relay,HIGH);//led off
  while (assume<=0){//while true
    if (digitalRead(Lim1)==LOW){
      //cw,lim1
      digitalWrite(Hb1,LOW);
      digitalWrite(Hb2,HIGH);
      analogWrite(HbPwm,255);
    }
    if (digitalRead(Lim1)==HIGH){
      //ccw,lim2
      analogWrite(HbPwm,0);
      //delay(500);
      digitalWrite(Hb1,HIGH);
      digitalWrite(Hb2,LOW);
      analogWrite(HbPwm,255);
      delay(tohome);//to home 90 deg
      analogWrite(HbPwm,0);
      assume=assume+1;//break while true
      break;
    }
  }
  myservo.write(80);//servo normal level
  
  //if ir 1 and ir 2 notfound an object -> led off
  while ((digitalRead(Ir2)==HIGH ) and (digitalRead(Ir1)==HIGH)){
    digitalWrite(Relay,HIGH);//led off
  }
  //if ir1 or 2 found an object (exit from loop while)
  digitalWrite(Relay,LOW);//led on
  while (assume2<=0){
    if (digitalRead(LedPlas)==HIGH){
      digitalWrite(Relay,HIGH);//led off
      myservo.write(125);
      delay(500);
      myservo.write(80);
      break;
    }
    if (digitalRead(LedOthers)==HIGH){
      digitalWrite(Relay,HIGH);//led off
      myservo.write(0);
      delay(500);
      myservo.write(80);
      break;
    }
    if (digitalRead(LedAl)==HIGH){
      digitalWrite(Relay,HIGH);//led off
      while (digitalRead(Lim1)==LOW){
        //cw,lim1
        digitalWrite(Hb1,LOW);
        digitalWrite(Hb2,HIGH);
        analogWrite(HbPwm,255);
      }
      analogWrite(HbPwm,0);
      myservo.write(125);
      delay(500);
      digitalWrite(Hb1,HIGH);
      digitalWrite(Hb2,LOW);
      analogWrite(HbPwm,255);
      delay(tohome); //to home
      analogWrite(HbPwm,0);
      myservo.write(80);
      break;
    }
    if (digitalRead(LedPaper)==HIGH){
      digitalWrite(Relay,HIGH);//led off
      while (digitalRead(Lim2)==LOW){
        //ccw,lim2
        digitalWrite(Hb1,HIGH);
        digitalWrite(Hb2,LOW);
        analogWrite(HbPwm,255);
       }
       analogWrite(HbPwm,0);
       myservo.write(125);
       delay(500);
       digitalWrite(Hb1,LOW);
       digitalWrite(Hb2,HIGH);
       analogWrite(HbPwm,255);
       delay(tohome); //to home
       analogWrite(HbPwm,0);
       myservo.write(80);
       break;
    }
  }
 
  }
  

      

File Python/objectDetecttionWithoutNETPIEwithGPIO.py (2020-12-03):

######## Picamera Object Detection Using Tensorflow Classifier #########
#
# Author: Evan Juras
# Date: 4/15/18
# Description: 
# This program uses a TensorFlow classifier to perform object detection.
# It loads the classifier uses it to perform object detection on a Picamera feed.
# It draws boxes and scores around the objects of interest in each frame from
# the Picamera. It also can be used with a webcam by adding "--usbcam"
# when executing this script from the terminal.

## Some of the code is copied from Google's example at
## https://github.com/tensorflow/models/blob/master/research/object_detection/object_detection_tutorial.ipynb

## and some is copied from Dat Tran's example at
## https://github.com/datitran/object_detector_app/blob/master/object_detection_app.py

## but I changed it to make it more understandable to me.


# Import packages
import os
import cv2
import numpy as np
from picamera.array import PiRGBArray
from picamera import PiCamera
import tensorflow as tf
import argparse
import sys
#gpio
import RPi.GPIO as GPIO
import time

#microgear
#import microgear.client as microgear



# Set up camera constants
IM_WIDTH = 640
IM_HEIGHT = 480
#IM_WIDTH = 640    Use smaller resolution for,initial=1280
#IM_HEIGHT = 480   slightly faster framerate,initial=720

# Select camera type (if user enters --usbcam when calling this script,
# a USB webcam will be used)
camera_type = 'picamera'
parser = argparse.ArgumentParser()
parser.add_argument('--usbcam', help='Use a USB webcam instead of picamera',
                    action='store_true')
args = parser.parse_args()
if args.usbcam:
    camera_type = 'usb'

# This is needed since the working directory is the object_detection folder.
sys.path.append('..')

# Import utilites
from utils import label_map_util
from utils import visualization_utils as vis_util

# Name of the directory containing the object detection module we're using
MODEL_NAME = 'Trash2'
#initail = 'ssdlite_mobilenet_v2_coco_2018_05_09lol','card_model'

# Grab path to current working directory
CWD_PATH = os.getcwd()

# Path to frozen detection graph .pb file, which contains the model that is used
# for object detection.
PATH_TO_CKPT = os.path.join(CWD_PATH,MODEL_NAME,'frozen_inference_graph.pb')

# Path to label map file
PATH_TO_LABELS = os.path.join(CWD_PATH,'data','label_mapTrash2.pbtxt')
#initial='mscoco_label_mapTrash.pbtxt','card_labelmap.pbtxt'

# Number of classes the object detector can identify
NUM_CLASSES = 5
#initila=90 , 13

## Load the label map.
# Label maps map indices to category names, so that when the convolution
# network predicts `5`, we know that this corresponds to `airplane`.
# Here we use internal utility functions, but anything that returns a
# dictionary mapping integers to appropriate string labels would be fine
label_map = label_map_util.load_labelmap(PATH_TO_LABELS)
categories = label_map_util.convert_label_map_to_categories(label_map, max_num_classes=NUM_CLASSES, use_display_name=True)
category_index = label_map_util.create_category_index(categories)


# Load the Tensorflow model into memory.
detection_graph = tf.Graph()
with detection_graph.as_default():
    od_graph_def = tf.GraphDef()
    with tf.gfile.GFile(PATH_TO_CKPT, 'rb') as fid:
        serialized_graph = fid.read()
        od_graph_def.ParseFromString(serialized_graph)
        tf.import_graph_def(od_graph_def, name='')

    sess = tf.Session(graph=detection_graph)


# Define input and output tensors (i.e. data) for the object detection classifier

# Input tensor is the image
image_tensor = detection_graph.get_tensor_by_name('image_tensor:0')

# Output tensors are the detection boxes, scores, and classes
# Each box represents a part of the image where a particular object was detected
detection_boxes = detection_graph.get_tensor_by_name('detection_boxes:0')

# Each score represents level of confidence for each of the objects.
# The score is shown on the result image, together with the class label.
detection_scores = detection_graph.get_tensor_by_name('detection_scores:0')
detection_classes = detection_graph.get_tensor_by_name('detection_classes:0')


# Number of objects detected
num_detections = detection_graph.get_tensor_by_name('num_detections:0')

# Initialize frame rate calculation
frame_rate_calc = 1
freq = cv2.getTickFrequency()
font = cv2.FONT_HERSHEY_SIMPLEX

# Initialize camera and perform object detection.
# The camera has to be set up and used differently depending on if it's a
# Picamera or USB webcam.

# I know this is ugly, but I basically copy+pasted the code for the object
# detection loop twice, and made one work for Picamera and the other work
# for USB.
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
